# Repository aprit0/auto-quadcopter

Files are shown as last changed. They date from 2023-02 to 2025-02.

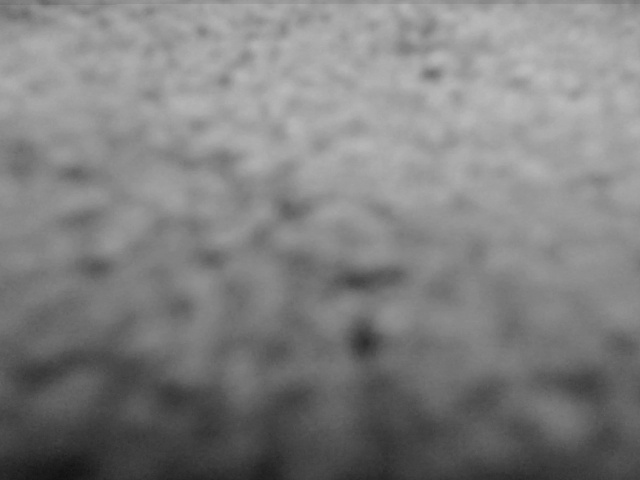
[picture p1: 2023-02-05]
auto-quadcopter/1_PYTHON_TEST/sensors/test_grey.jpg

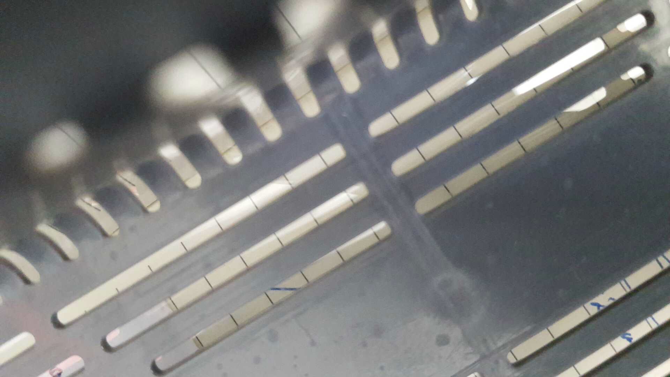
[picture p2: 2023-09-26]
auto-quadcopter/Drone/devices/camera.jpg

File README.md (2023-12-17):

# Autonomous Quadcopter
  An autonomous drone designed for semi autonomous flight. As I am no flying wiz, skill is supplemented with software! 
## STATUS
- [x] Build prototype hardware
- [x] Code and integrate flight controller sensors
- [x] Code and integrate base station
- [x] Roll/Pitch/Yaw PID Tuning
- [x] FIRST FLIGHT  
- [~] Code and integrate XYZ Hover - Awaiting Optical Flow Sensor  
- [ ] STABLE PLATFORM FLIGHT
- [x] Code and integrate GPS
- [ ] ROS RANGE TEST FLIGHT

## Small Scale Task Tracking
- [ ] Validate sensors in RVIZ 
-   [ ] Ensure OF twist is in the correct orientation and is un 

## Bugs
- [ ] BMS Current Sensor 

# Background
## Main
  Utilising a self developed flight controller, rpi controls the drone and interacts with the base over ROS.  
  
## Multiwii
  A combination of rpi brain, arduino nano receiving i2c commands and transferring them over PPM to an arduino running MultiWii. The benefit was supposed to be reduced development time with an out of the box open source solution. Due to numerous issues, compatability and expanding hardware requirements this method was tried first and dropped.  

## Arduino
  A tested combination of rpi brain and arduino pwm/C based loop. Due to i2c redundancies, the arduino was shown to be not required. As I was using an arduino nano, the hardware speed is too low to provide a meaningful benefit. This method was tried second and dropped in favour of a complete pi based drone.  

# Project Overview:
Using ROS2 nodes, the code base can be easily modular, adaptable and upgradeable. The simple wifi streaming of data allows for high quality communications at the cost of range.

## Base Station
| Component | Hardware | Software |
| :--- | :--- | :--- |
| Base Station | XBOX Controller, Laptop, Router | joystick_node |

## Drone
| Component | Hardware | Software |
| :--- | :--- | :--- |
| Base Flight Controller | RPi, BNO085 9DOF IMU | control_node, devices_node |
| XYZ Hover Control | USB2.0 Webcam, VL53L0X, MPL3115A2 Altimeter, (IMU) | TBD |
| GPS | BN880Q - Future RTX GPS? | devices_node |
| Camera Feed | Analogue Camera, TX, RX, Android Phone | N/A |
| BMS | Self Designed PCB | TBD: I2C |

## Features
- XYZ Stabilisation with optical flow
- Benefits of ROS ecosystem

## Conventions
- Orientation/Units: [REP103](https://www.ros.org/reps/rep-0103.html)

# Installation
## Dependencies
TOF: https://github.com/Gadgetoid/VL53L0X-python/blob/master/python/VL53L0X.py
..

## Boot
crontab -e, "@reboot ~/ros2_ws/src/auto-quadcopter/boot.sh"

# Learnings
## Optical Flow
This algorithm was coded and implemented. Loop speed was reasonable at 60Hz and able to accurately track magnitude and directions with both sparse and dense flow algorithms.   
Limitation: The hardware used was a webcam, this was limited to 30Hz BUT *Auto focus could cause every second image to be blurred*  
Fix: Buy Optical Flow hardware for lateral velocity

# Ros
## Handy lines
```
ros2 topic pub -r 10 base/ARM std_msgs/msg/Bool "{data: True}" 
```

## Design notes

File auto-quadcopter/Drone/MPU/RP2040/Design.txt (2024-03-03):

Aim: Isolated Flight Controller

Messages
In: 
- Set Throttle and angles
A{T:[1000,2000,1], R:[-90.1, 90.0, 0.1], P:[-90.0, 90.0, 0.1], Y:[-180.0, 180.0, 0.1]}
- Set PID Values
B{P: 0.1, I:0.1, D:0.1}
- Set arm
C{A:[0,1]}

Out:
- Get PID Values
Z{P: 0.1, I:0.1, D:0.1}
- Get angles
Y{R:[-90.1, 90.0, 0.1], P:[-90.0, 90.0, 0.1], Y:[-180.0, 180.0, 0.1]}
- Status
X{S:[0,9]}
0:Not Ready
1:Ready
2:IMU Error

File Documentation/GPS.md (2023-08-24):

# BN-880Q
Setup: https://www.engineersgarage.com/articles-raspberry-pi-neo-6m-gps-module-interfacing/  
U-Centre: https://oscarliang.com/gps-settings-u-center/

RPI U-Boot Autoboot to avoid RX Pin overload:
1. Connect to your Pi with a serial console (for example using screen):
2. Abort the boot process through pressing a key and set the bootdelay variable to -2:
3. `U-Boot> setenv bootdelay -2`
4. `U-Boot> saveenv`

# To Test
CPO May offer single module millimetre precision
- https://github.com/utiasASRL/cpo

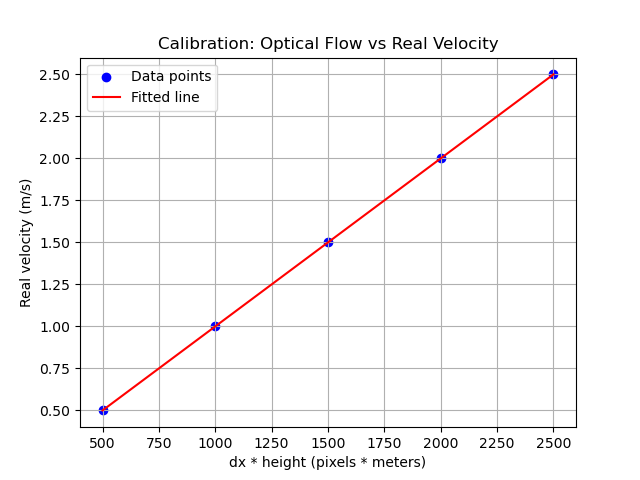
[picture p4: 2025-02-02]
auto-quadcopter/abc.png

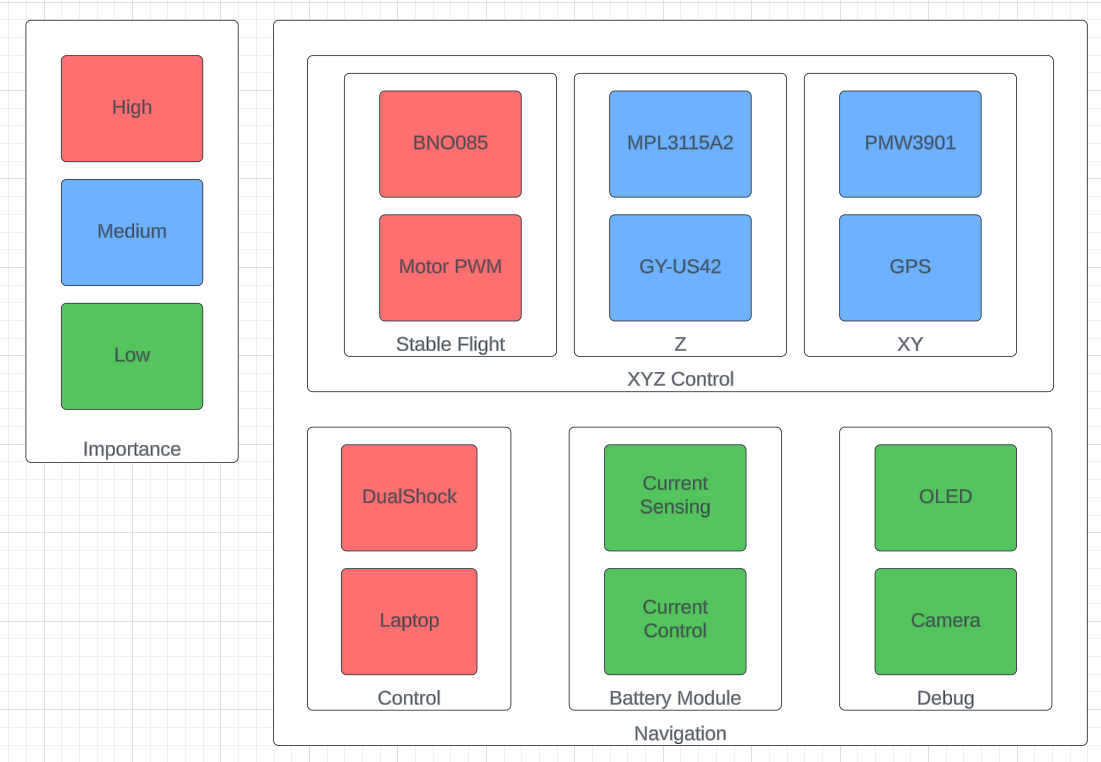
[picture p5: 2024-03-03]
Documentation/Planning/priority.png

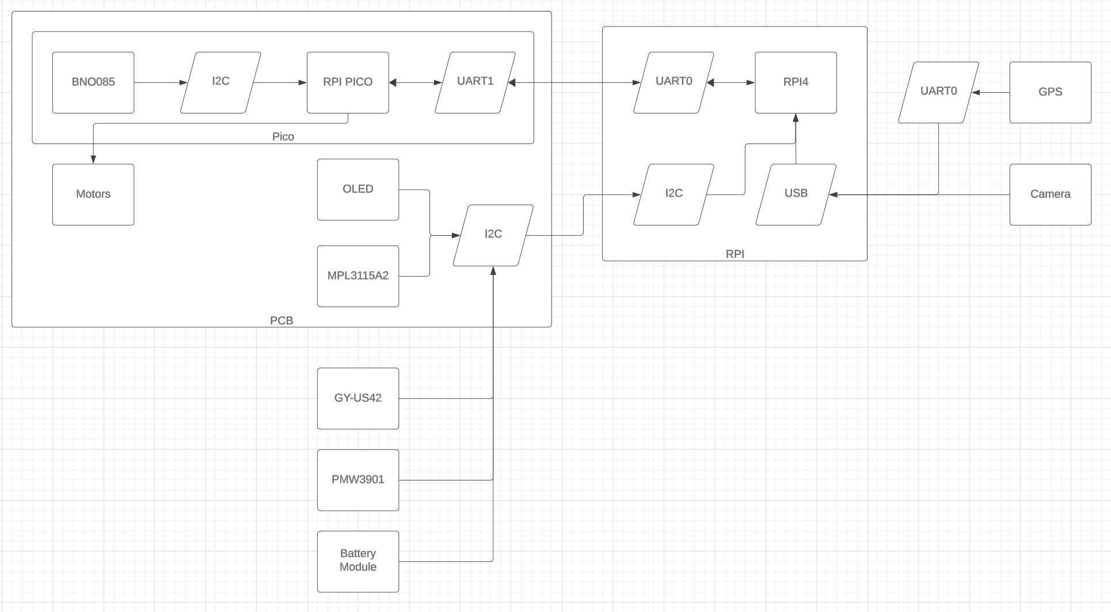
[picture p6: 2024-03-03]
Documentation/Planning/pcb.png

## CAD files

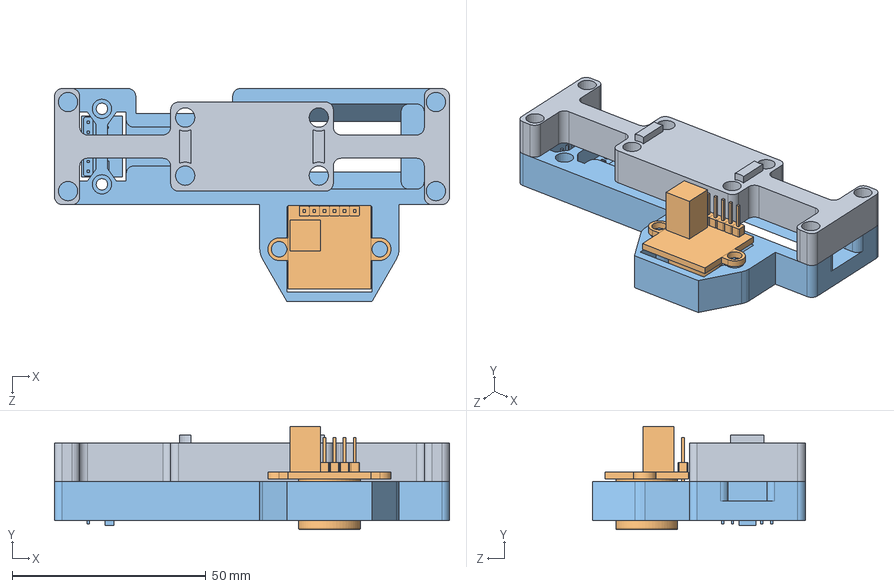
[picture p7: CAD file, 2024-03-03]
Documentation/CAD/V0_SensorBreakout/Assem1.SLDASM
102.0 x 26.6 x 55.0 mm
mount
GY-US42 ULTERASONIC madule
cover_3

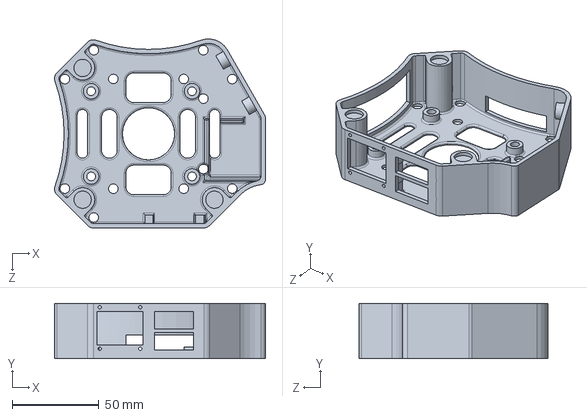
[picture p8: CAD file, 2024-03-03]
Documentation/CAD/V0_Mount/mount1.SLDPRT
121.3 x 31.6 x 108.5 mm

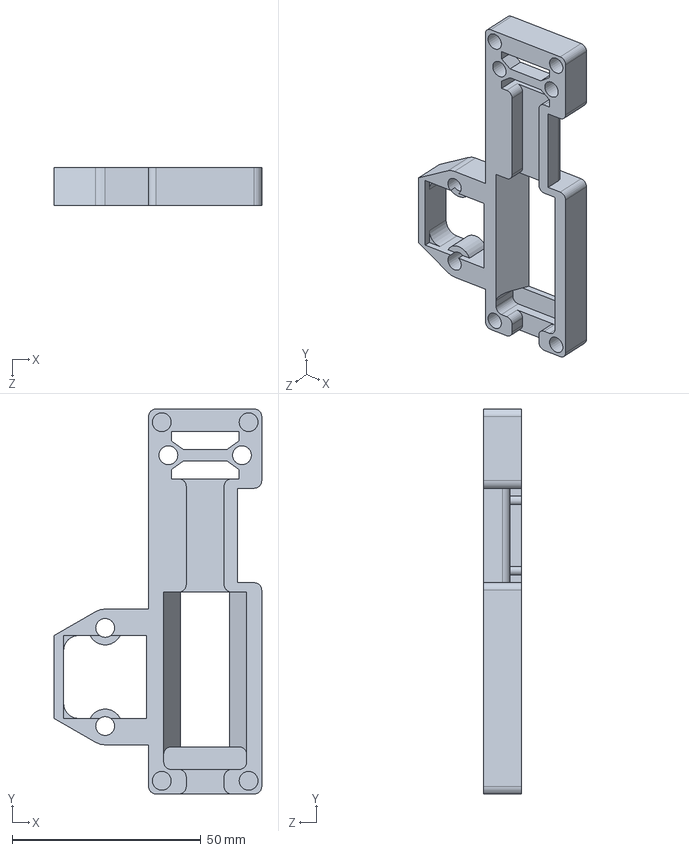
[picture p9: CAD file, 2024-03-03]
Documentation/CAD/V0_SensorBreakout/cover_3.SLDPRT
55.0 x 102.0 x 10.0 mm

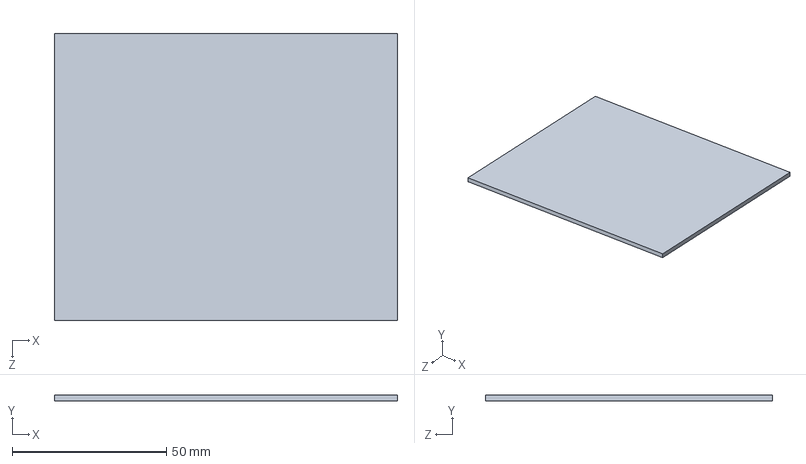
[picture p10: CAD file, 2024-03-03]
Documentation/CAD/V0_Mount/mount.SLDPRT
111.1 x 2.00 x 93.0 mm

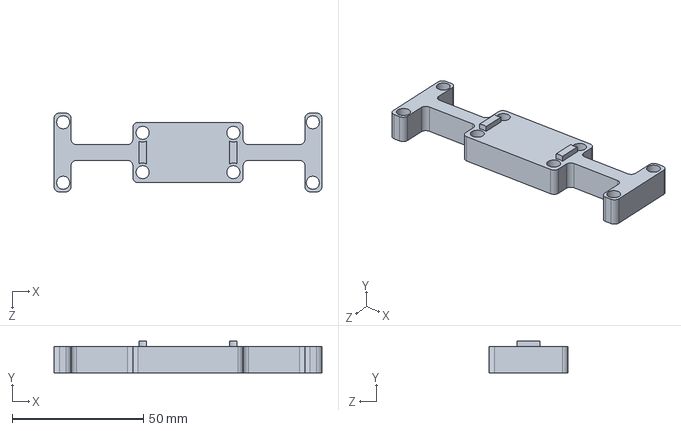
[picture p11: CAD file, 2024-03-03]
Documentation/CAD/V0_SensorBreakout/mount.SLDPRT
102.0 x 12.0 x 30.0 mm

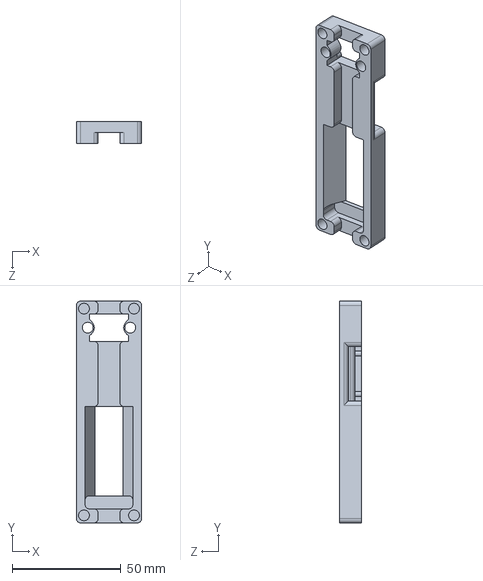
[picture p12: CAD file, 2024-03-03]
Documentation/CAD/V0_SensorBreakout/cover_2.SLDPRT
30.0 x 102.0 x 10.0 mm

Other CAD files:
Documentation/CAD/V0_Mount/mount1.STL
Documentation/CAD/V0_SensorBreakout/cover_3.STL

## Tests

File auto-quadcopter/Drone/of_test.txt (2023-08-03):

Use GPS? (0|1)Use GPS? (0|1)0 0 0.2
0 0 0.2
0 0 0.2
0 0 0.22
0 0 0.22
0 0 0.22
2 2 0.25
2 2 0.25
0 0 0.25
-1 -1 0.32
-2 1 0.32
-4 -1 0.35000000000000003
1 -1 0.35000000000000003
-15 0 0.35000000000000003
-8 1 0.35000000000000003
-8 -1 0.35000000000000003
-9 2 0.35000000000000003
-16 8 0.34
-18 1 0.34
-17 0 0.34
-21 6 0.34
-25 3 0.34
-22 -4 0.34
-24 -7 0.34
-22 -3 0.34
-23 -1 0.34
-18 0 0.34
-21 -2 0.34
-11 -3 0.34
-6 -4 0.34
-1 -4 0.49
-5 -5 0.49
-11 -2 0.51
-16 0 0.51
-15 1 0.51
-11 1 0.92
-11 1 0.92
-3 0 0.92
-1 0 0.99
-3 0 0.99
-7 0 0.99
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

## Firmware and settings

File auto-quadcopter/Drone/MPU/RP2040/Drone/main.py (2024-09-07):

import asyncio
import json
import math as m
import time
from communication import PICO2PI
from motors import MOTORS
from pid import FC_PID
from sensors import INERTIAL




class FlightController(PICO2PI):
    PID_FILENAME = "PID_CALIB.json"
    THROTTLE_BASE = 1000
    TEST_LIMIT = 1200
    def __init__(self, test_mode=False):
        self.euler_setpoints = [0] * 3
        self.throttle_setpoint = 1000
        self.euler_current = [None] * 3
        self.ARM = False
        self.test_mode = test_mode
        super().__init__()

        # PID
        self.P, self.I, self.D = None, None, None
        self.pid = FC_PID()
        self.load_pid()

        # Sensors
        self.imu = INERTIAL()

        # Motors
        self.motors = MOTORS()
        
    async def main(self):
        if self.test_mode:
            self.set_arm({"any_value": True})
        while True:
            self.euler_current = self.imu.read()
            y_new = self.euler_setpoints[2] - self.euler_current[2]
            yaw_dist = y_new if abs(y_new) < 180 else y_new + (-1 * m.copysign(1, y_new) * 360)
            pid_out = self.pid.run(self.euler_current[:2]+[yaw_dist])
            # print("main euler: ", self.euler_current[:2], yaw_dist)
            if self.pid.enabled or self.test_mode:
                # print("main pid: ", self.throttle_setpoint, pid_out)
                '''
                self.euler_current = [roll, pitch] + [yaw]
                roll: +ive euler, LHS Up, RHS Down, LHS less speed, RHS more speed, pid more negative
                pitch: +ve euler, Back Up, Front Down, Back less speed, Front more speed, pid more negative 
                '''
                fl = self.throttle_setpoint + pid_out[0] - pid_out[1] #+ pid_out[2]
                fr = self.throttle_setpoint - pid_out[0] - pid_out[1] #- pid_out[2]
                br = self.throttle_setpoint - pid_out[0] + pid_out[1] #+ pid_out[2]
                bl = self.throttle_setpoint + pid_out[0] + pid_out[1] #- pid_out[2]
                if self.test_mode:
                    [fl, fr, br, bl] = [min(self.TEST_LIMIT, i) for i in [fl, fr, br, bl]]
            else:
                fl, fr, bl, br = self.THROTTLE_BASE, self.THROTTLE_BASE, self.THROTTLE_BASE, self.THROTTLE_BASE 
            self.motors.set_speed(fl, fr, bl, br, self.ARM)
            await asyncio.sleep(0)
        
    def set_setpoints(self, msg):
        self.throttle_setpoint = int(msg["T"])
        self.euler_setpoints = [float(msg[key]) for key in ["R", "P", "Y"]]
        self.euler_setpoints[2] = self.euler_setpoints[2] if abs(self.euler_setpoints[2]) < 180 else self.euler_setpoints[2] + (-1 * m.copysign(1, self.euler_setpoints[2]) * 360) 
        self.pid.set_euler_setpoints([i for i in self.euler_setpoints])

    def set_arm(self, msg):
        self.ARM = bool(int(list(msg.values())[0]))
        if self.ARM:
            self.pid.pid_enable()
        else:
            self.pid.pid_disable()
        
    def write_config(self, _msg):
        self.write_pid()

    def get_pid_setpoints(self, _msg):
        out = self.pid.get_params()
        # self.set_log(out)
        self.write_msg("get_pid_setpoints", {i:j for i, j in zip(["P", "I", "D"], out)})

        
    def get_pose(self, _msg):
        # print("pose")
        out_dict = {key: round(value, 1) for key, value in zip(["R", "P", "Y"], self.euler_current)}
        self.write_msg("get_pose", out_dict)

    def load_pid(self):
        f = open(self.PID_FILENAME)
        out = json.load(f)
        for key in out:
            setattr(self, key, out[key])
        self.pid.set_params(self.P, self.I, self.D)

    def set_pid_setpoints(self, msg):
        out = list(msg.items())
        # self.set_log(out)
        for (key, value) in out:
            setattr(self, key, float(value))
        self.pid.set_params(self.P, self.I, self.D)
        # print(self.pid.kp)
        
    def write_pid(self):
        pid_out = {key: value for key, value in zip(["P", "I", "D"], self.pid.get_params())} 
        # print(pid_out)
        with open(self.PID_FILENAME, "w") as f:
            json.dump(pid_out, f)


def custom_exception_handler(loop, context):
    print(context)
    loop.default_exception_handler(context)
    loop.stop()

if __name__ == "__main__":
    FC = FlightController(False)
    loop = asyncio.get_event_loop()
    # loop.set_exception_handler(custom_exception_handler)
    loop.create_task(FC.main())
    # loop.create_task(FC.read_serial())
    loop.create_task(FC.update_state())
    loop.create_task(FC.sender())
    loop.create_task(FC.receiver())
    loop.run_forever()

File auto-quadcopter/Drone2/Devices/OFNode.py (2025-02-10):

import rclpy
from rclpy.node import Node
from geometry_msgs.msg import Twist
from std_msgs.msg import Float32MultiArray, Float32
import math
import serial
import time

class OpticalFlowVelocityNode(Node):
    def __init__(self):
        super().__init__('optical_flow_velocity_node')

        # Publisher for velocity in x and y directions
        self.velocity_publisher = self.create_publisher(Twist, 'drone/dev/velocity', 10)
        self.z_publisher = self.create_publisher(Float32, 'drone/dev/z', 10)

        # Subscriber for Euler angles (roll, pitch, yaw) in degrees
        self.euler_angles_subscriber = self.create_subscription(
            Float32MultiArray,
            'drone/dev/euler',
            self.euler_angles_callback,
            10
        )
        f = open("/home/pi/ros2_ws/src/auto-quadcopter/auto-quadcopter/1_PYTHON_TEST/OpticalFlow/readings.txt", "w")
        f.close()
        self.write("dt,self.z,dz,self.tof_height},self.us_height},self.roll},{self.pitch,self.dx},{self.dy,{dist_x,{dist_y\n")

        # Timer to periodically publish velocity
        self.timer = self.create_timer(0.01, self.publish_velocity)  # Timer for 10 Hz (0.1s interval)

        # Serial port setup to read data from /dev/ttyUSB0
        self.serial_port = "/dev/serial/by-id/usb-1a86_USB_Serial-if00-port0"
        self.ser = serial.Serial(self.serial_port, 115200, timeout=1)  # Adjust the baud rate if needed
        time.sleep(2)  # Wait for the serial connection to initialize

        # Example variables for calculation (these should be updated with actual sensor data)
        self.last_data = None
        self.current_data = None
        self.z = 0
        self.dz = 0
        self.dt = 0
        self.dx = 0.0
        self.dy = 0.0
        self.px = 0.0
        self.py = 0.0
        self.us_height = 0  # height from TOF sensor (in meters)
        self.us_velocity = 0  # height from pressure sensor (in meters)
        self.pressure_height = 0  # height from pressure sensor (in meters)
        self.pressure_velocity = 0  # height from TOF sensor (in meters)
        self.tof_height = 0  # height from TOF sensor (in meters)
        self.tof_velocity = 0  # height from pressure sensor (in meters)
        self.roll = 0.0  # roll angle in radians
        self.pitch = 0.0  # pitch angle in radians
        self.yaw = 0.0  # yaw angle in radians
    def write(self, msg):
        f = open("/home/pi/ros2_ws/src/auto-quadcopter/auto-quadcopter/1_PYTHON_TEST/OpticalFlow/readings.txt", "a")
        f.write(msg)
        f.close()

    def euler_angles_callback(self, msg):
        """
        Callback to update roll, pitch, and yaw from the subscribed message.
        The angles are in degrees, so we convert them to radians.
        """
        if len(msg.data) == 3:
            self.roll = math.radians(msg.data[0])  # Convert roll from degrees to radians
            self.pitch = math.radians(msg.data[1])  # Convert pitch from degrees to radians
            self.yaw = math.radians(msg.data[2])  # Convert yaw from degrees to radians
            # self.get_logger().info(f"Received Euler angles: roll={msg.data[0]}°, pitch={msg.data[1]}°, yaw={msg.data[2]}°")

    def read_serial_data(self):
        """
        Read data from the serial port. This function assumes that the data is in a comma-separated
        format, and it can be customized based on your actual serial data format.
        """
        try:
            while self.ser.in_waiting > 0:
                # Read a line from the serial port
                line = self.ser.readline().decode('utf-8').strip()
                self.get_logger().info(f"Serial data received: {line}")
                # Parse the data (e.g., optical flow dx, dy, and heights)
                data = [float(i) for i in line.split(',')]
                # dt	us_height	us_velocity	pressure_height	pressure_velocity	tof_height	tof_velocity	dx	dy
                self.last_data = self.current_data
                self.current_data = data
                [self.dt, self.us_height, self.us_velocity, self.pressure_height, self.pressure_velocity, self.tof_height, self.tof_velocity, self.px, self.py] = self.current_data
                _ = self.calculate_velocity_from_optical_flow()
            # else:
                # self.dt = 0
        except Exception as e:
            self.get_logger().warn(f"Failed to read serial data: {str(e)}")

    def calculate_true_height(self, tof_limit=2, us_limit=4):
        # Kinematics model to smooth tof_height
        z_est = self.z + self.dz * self.last_data[0] / 1000
        if self.current_data[5] > tof_limit and self.current_data[1] < us_limit:
            if not (z_est * 1.2 > self.current_data[1] > z_est * 0.8):
                # If the us value is significantly different to the estimated value, and we are in low level flight
                return z_est
        return self.tof_height if self.tof_height < tof_limit else self.us_height if self.us_height < us_limit else self.pressure_height, z_est




    def calculate_velocity_from_optical_flow(self, tof_limit=2, us_limit=4):
        """
        Calculate the velocity in the x and y directions from optical flow and sensor height.
        """
        
        true_height, z_est = self.calculate_true_height()
        self.dz = (true_height - self.z) / self.dt / 1000
        self.z = true_height
        # true_height = self.tof_height if self.tof_height < tof_limit else self.us_height if self.us_height < us_limit else self.pressure_height
        if true_height != self.pressure_height:
            true_height *= math.cos(self.pitch) * math.cos(self.roll)
            
        scaling_factor = (true_height / (35 * 10)) * 2 * math.tan(math.radians(42)/2)
        dist_x = self.px * scaling_factor
        dist_y = self.py * scaling_factor
        self.dx = dist_x / (self.dt / 1000)
        self.dy = dist_y / (self.dt / 1000)

        print(f"{self.dt},{self.z},{self.dz},{self.roll},{self.pitch},{self.dx},{self.dy}")
        self.write(f"{self.dt},{self.z},{self.dz},{self.roll},{self.pitch},{self.dx},{self.dy}\n")

    def publish_velocity(self):
        # Read serial data (optical flow and heights)
        self.read_serial_data()
        # Calculate the velocities from the optical flow and sensor data
        if self.z != None:
            # velocity_x, velocity_y = self.calculate_velocity_from_optical_flow()
            
            # # Create a Twist message to hold the velocity information
            velocity_msg = Twist()
            velocity_msg.linear.x = self.dx
            velocity_msg.linear.y = self.dy
            velocity_msg.linear.z = float(self.dz)
            
            z_msg = Float32()
            z_msg.data = float(self.z)

            # Publish the velocity message
            self.velocity_publisher.publish(velocity_msg)
            self.z_publisher.publish(z_msg)
            self.get_logger().info(f"Published velocity - x: {self.dx:.2f} m/s, y: {self.dx:.2f} m/s")
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

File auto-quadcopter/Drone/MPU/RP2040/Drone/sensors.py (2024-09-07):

from adafruit_bno08x.i2c import BNO08X_I2C
from adafruit_bno08x import (
    BNO_REPORT_ROTATION_VECTOR,
    BNO_REPORT_GYROSCOPE,
    BNO_REPORT_LINEAR_ACCELERATION
)
from utils import quat_2_euler
import busio, board


class INERTIAL(BNO08X_I2C):
    def __init__(self) -> None:
        self.i2c = busio.I2C(board.GP3, board.GP2,frequency=400000)
        super().__init__(self.i2c)
        self.enable_feature(BNO_REPORT_ROTATION_VECTOR)
        self.enable_feature(BNO_REPORT_GYROSCOPE)
        self.enable_feature(BNO_REPORT_LINEAR_ACCELERATION)

        self.quat = None
        self.euler = None
        pass


    def read(self):
        i, j, k, w = self.quaternion
        self.quat = [i, j, k, w]
        r, p, y = quat_2_euler(i, j, k, w)
        self.euler = [r, p, y] 
        # print(self.euler)
        return self.euler
        # return [0,0,1]
                 

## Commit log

2023-01-12 updated for new imu
2023-01-18 pid testing on roll axis only
2023-01-22 optical flow calcs
2023-01-22 Optical Flow script
2023-01-28 IMU Pose complete, OF not. *Planner* Planned
    [OF_Calib.csv]
2023-01-30 Non blocking sensors
    [OF_Calib.csv]
2023-02-11 pico i2c slave support
2023-02-11 i2c pico interface
2023-02-12 OF calib script ready, pico integrated
2023-02-12 pico i2c encoding formula and main update
    [byte_scaling.xlsx]
2023-03-29 implement ultrasonic transceiver instead of tof
    [OF_calib.csv]
2023-05-07 begin velocity control
2023-05-17 add arduino and edit boot
2023-05-17 Add arduino code
2023-05-18 update hardware and arduino
2023-08-22 add foxglove
    [OF_Calib.csv, OF_calib.csv]
2023-09-26 Added ip camera and localization functionality
2024-02-25 RPI PICO
    [bn880Q_config.txt]
2024-03-03 add cad and pico
    [Assem1.SLDASM, PID_CALIB.json, cover_2.SLDPRT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]
2024-03-05 pico improvements
2024-03-07 pico main edit
2024-03-10 update PICO
